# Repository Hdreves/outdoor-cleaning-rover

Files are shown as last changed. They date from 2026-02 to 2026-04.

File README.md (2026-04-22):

# Outdoor Cleaning Rover

## Project Description

Outdoor Cleaning Rover is a shoebox-sized keyboard/webpage controlled robot designed to patrol a patio and sidewalk and collect dog waste using a small “garbage-truck” style scoop. The rover navigates outdoors at low speed and can pickup waste when seen on camera. The project integrates embedded control, sensing, and vision hardware, powered through a LiPo battery.

**High-level goals**
- Drive safely on concrete/pavers.
- Detect a target/object and perform a pickup routine.
- Deposit waste into a bin for easy removal.

---

## Problem Domain

Pet waste on patios and sidewalks is unpleasant, unsanitary, and easy to miss especially at night or when the yard/patio is large. Owners often delay cleanup, which can create health risks (bacteria/parasites), odors, and messy tracking into the home. A small rover that can periodically patrol and collect waste reduces the burden on owners and keeps outdoor spaces clean.

---

## Features and Requirements

### Features & Requirements

1. Remote Control
   - Controlled through a webpage or keyboard

2. Pickup Mechanism (Garbage-Truck Scoop)
   - A front scoop lowers, collects waste, and deposits into a bin

3. Interactive Webpage
   - Updates with rover movements and sensor readings

4. Power Management
   - Battery-powered operation with regulated rails for logic and actuators

---

## Architecture

### System Overview

- **ESP32 (3.3V)** — Main controller (“brains”)
  - High-level behavior/state machine
  - Sensor fusion / navigation logic
  - Receives commands from Raspberry Pi
  - Sends motor/servo commands
 
- **Raspberry Pi** — Web interface, camera streaming, and high-level user interaction
  - Hosts the webpage/control dashboard
  - Streams live camera feed from the Pi Camera
  - Sends user control commands to the ESP32
  - Displays rover status and sensor feedback

- **Motor Driver (Dual H-Bridge)**
  - Drives left and right DC gear motors

- **Sensors**
  - ToF distance sensor for obstacle detection
  - Wheel encoders (for distance/heading estimation)

- **Actuators**
  - DC motors (drive)
  - Servo

- **Power**
  - 3S battery → main switch
  - Buck converter to regulated 5V rail
  - Motors powered from battery rail (through driver), logic from regulated rail
  - Common ground shared across all modules

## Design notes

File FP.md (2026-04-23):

---
marp: true
theme: default
paginate: true
size: 16:9
---

# CSC 494 Final Presentation  
## Outdoor Cleaning Rover

**Hunter Dreves** 

**CSC 494**  

---

# Project Overview

## Problem Domain
Outdoor pet waste cleanup.

 The goal was to create a rover that can move around outside, perform the task of picking up pet waste, and put it in a bin. This prevents having to do it manually by hand and dealing with the cleanup. This problem combined power distribution, mechanical design, sensing, and control logic in order to come up with a solution.

---

# Solution Domain

A robotic system that combines hardware and software to perform the task of waste cleanup.

My solution uses a small rover with motors, a scoop/dump mechanism powered by a servo, a breadboard housing ESP32 and VL53L0X sensor, a Raspberry Pi, DC convertors for Pi and servo, and a camera to see where the rover is moving.

---

# Progress Since S1P

## At S1P
- chassis was assembled
- Raspberry Pi was set up with camera and SSH
- breadboard and wiring were partially started

## FP
- Week 1: Soldered and wired sensors, started designing parts
- Week 2: Created webpage to interface with rover, started main electrical wiring
- Week 3: Continued creating webpage while waiting for parts
- Week 4: Created wires and wire connectors

---
# Progress Since S1P

## FP
- Week 5: Re-created custom parts, finished all main wiring
- Week 6: Created sketch for ESP32, put everything together
- Week 7: Began testing and working out bugs
- Week 8: Testing and working out bugs
---

## Project links
- **Canvas:** https://nku.instructure.com/courses/88152/pages/individual-progress-hunter-dreves
- **GitHub:** https://github.com/Hdreves/outdoor-cleaning-rover/tree/main

---

# Movement Demo

[Open this file on GitHub](https://github.com/Hdreves/outdoor-cleaning-rover/blob/main/Media/Demos/Movement.mp4)

---

# Scooping Demo

[Open this file on GitHub](https://github.com/Hdreves/outdoor-cleaning-rover/blob/main/Media/Demos/Scooping.mp4)

---

# Dumping Demo

[Open this file on GitHub](https://github.com/Hdreves/outdoor-cleaning-rover/blob/main/Media/Demos/Dumping.mp4)

---

# Webpage 1

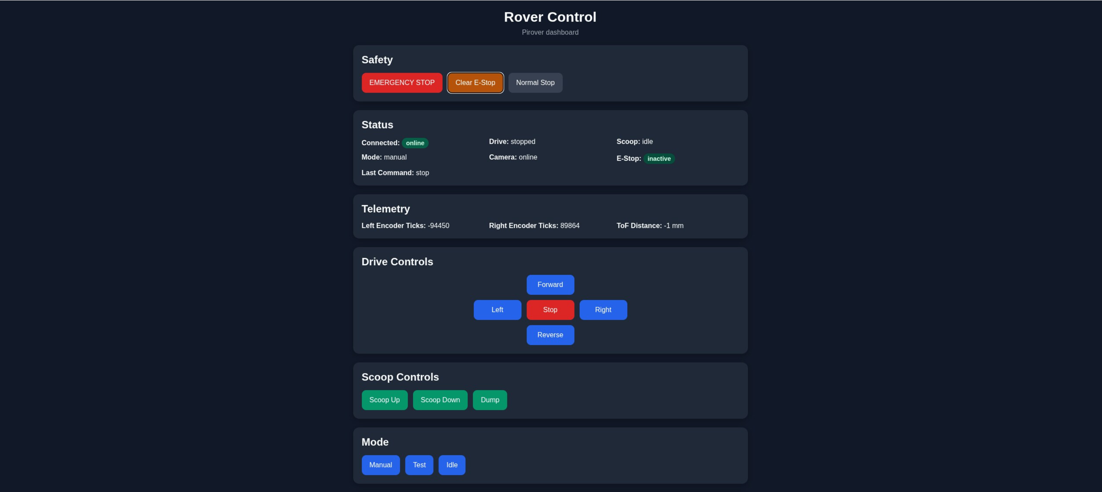
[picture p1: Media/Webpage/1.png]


---

# Webpage 2

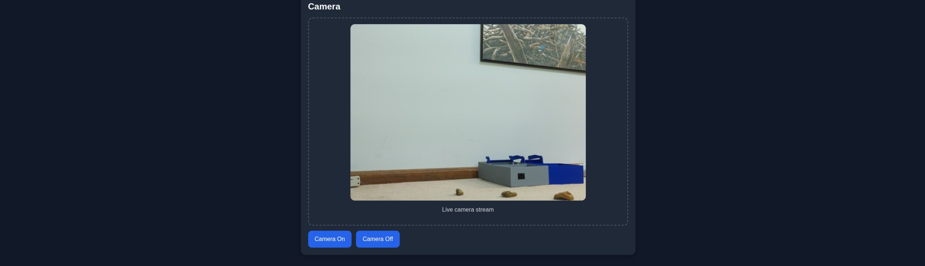
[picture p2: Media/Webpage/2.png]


---

# Learning With AI

## AI helped with
- Control logic design
- Debugging motors, sensors, and servo behavior
- Power distribution planning
- Code/setup guidance for integration

## Main lessons
- AI is useful for speeding up debugging
- AI struggles with mechanical designs
- AI is best used as a tool for support

---
# Topic 1

## Control Logic

The main takeaways when it comes to control logic is High level commands (Pi) need to be separated from low level commands (ESP32), pins need to be properly placed on ESP32, and not trying to force too much PWM control. With the Pi and ESP32 separated, debugging becomes much easier because you can isolate your issues. Also, ESP32 is much better at handling real time controls as that's what it was intended to do. Without proper pin placements, control goes out the window. You will run into problems like wrong motor movements, only one side moving, or nothing happening at all. When too many devices are being controlled through PWM, the devices will not function properly. Both devices are competing for timers/frequencies and in most cases one dominates the other. Also, devices use different timers/frequencies. For example, my servo (lower Hz) and DC motors (higher Hz), which lead to only the motors working. 

---
# Topic 2

## Power Distribution

The main takeaways when it comes to power distribution is sharing common ground, using convertors for lower rated electronics, and capacitors to prevent voltage spikes and drops. Without common ground signals are unreliable, sensors won't read or give bad values, random movements occur, or electrical damage. Without the use of convertors, a high voltage battery can fry your circut boards. The lower rated components can't handle the voltage supplied by the battery leading to failures and broken components. Capactitors come in handy for servos because sometimes voltage spikes and suddenly drops. During a voltage spike the capacitor stores that energy, and releases it during a moment of voltage drop.

---

# Issues Encountered and Solutions

## Issue 1: Wiring 
- Sensors not showing
- Wiring space
- Need for specific wires

## Solutions
- Used AI to determine sensor wasn't on shared ground
- Asked AI to help determine the dimensions for the box housing the elctrical components
- Had to cut, strip, and crimp the wires for my use case

--- 

## Issue 2: Hardware/Software Integration
- Motors moving incorrectly
- Values updating improperly
- Wheels continuosly moved after powering
- Servo wouldn't move

## Solutions
- Motors needed to be inverted
- Used AI to diagnose that there was interference when trying to use PWM for both the servo and motors. Moved the motors off of PWM and used digital direction signals through the motor driver instead.
---

## Issue 3: Design
- Initial design was much too complex
- Lack of space
- Reprint parts multiple times

## Soltuions
- Simplified the design
- Made space in any way possible, through creating holes and routing wires through them
- Modified incorrect parts and reprinted

---

# Questions

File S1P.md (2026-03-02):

---
marp: true
size: 4:3
paginate: true
---

# S1P  
## Outdoor Cleaning Rover

Hunter Dreves  

---

## Sprint 1 Progress

 **Chassis assembly**
- Rover chassis assembled (mechanical foundation complete)

 **Raspberry Pi Cam set up**
- SSH access configured for headless
- Camera connected and tested

 **Electronics groundwork**
- Breadboard layout for ESP (waiting on sensors should be in on 3/4)
- Planned separation of logic, servo, and motor power rails for safety

---

## Sprint 1 Progress

**Learned about hardware components and reliable power**
- 3s Lipo Battery (expected 3/4)
- 35 Kg servo (scoop and lift)
- 25 Kg servo (dump)
- VL53L0X TOF Sensors (2 meters, expected 3/4)
- 6V Buck converter for servos
- 5V Buck convertor for Pi
- Fuses
- Raspberry Pi (with Camera Module 3)

---

## Sprint 1 Progress
- Raspberry Pi (detection and navigation logic)
- ESP32-C6 (servos)

---

## Sprint 1 Learning with AI

### 1) Driving Controls
- Learned how control can be split between:
  - High-level decisions on Raspberry Pi (state machine)
  - Low-level motor/servo control (ESP32)

### 2) Power and Safe Wiring
- Learned importance of:
  - Separate power rails (motor vs servo vs logic)
  - Common ground
  - Fusing and switching
  - Avoiding brownouts

---

## What Changed From My Original Plan?

---

## Sprint 2 Final Goal

By end of Sprint 2, I will deliver a rover that:

- Manual control 
- Streams camera video from Raspberry Pi  
- Reads distance sensors for obstacle avoidance  
- Actuates the scoop mechanism on command  

**Stretch goals**
- Semi-autonomous navigation
- Target Detection

---

## Sprint 2 Plan

- Build 3-rail power architecture:
  - Motor rail (battery → fuse → switch → motor driver → motors)
  - Servo rail (battery → fuse → switch → 6V buck → servos)
  - Logic rail (battery → fuse → switch → 5V buck/USB-C → Pi + logic)
- Common ground + verify stability under load

---

## Sprint 2 Plan
- Wire VL53L0X ToF sensors on I2C
- Build UI for control
- Controlled tests

---

## Questions?

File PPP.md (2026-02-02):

---
marp: true
title: Outdoor Cleaning Rover — Project Plan
theme: default
paginate: true
size: 16:9
---

# Outdoor Cleaning Rover
## Project Plan Presentation (PPP)

**Shoebox-sized autonomous rover that patrols patio/sidewalk and collects dog waste** 

**Hunter Dreves
 CSC 494**

---

## Problem & Motivation

- Pet waste on patios/sidewalks is unsanitary and easy to miss
- Manual cleanup is time-consuming and often delayed
- A small rover can:
  - Patrol routinely
  - Avoid obstacles safely
  - Perform a pickup cycle

---
## Topics to Learn With AI

**Software:** Finite State Machines
  - Keeps the rovers movements organized and predictable.
  Prevents actions from overlapping and leadiing to errors.

**Hardware:** Power Distribution
  - Motors and servos create voltage dips.
  Without solid power distribution there 
  can be an increase in glitches.

---

## Sprint 1

- **How to power everything safely**
  - battery basics, turning the robot on/off, and keeping the electronics stable

- **How to make the rover move reliably**
  - drive forward/backward/turn and keep it controllable at a slow, safe speed

- **How to connect and read sensors**
  - distance sensors to “see” obstacles and bumpers as an emergency stop

- **How to test and troubleshoot**

---

## Sprint 2

- **Build the rover and pickup system**
  - a shoebox sized robot with a front scoop and a small bin so the rover can collect waste and store it

- **Make the scoop move automatically**
  - program the scoop to go down, collect, dump into the bin, then reset

- **Connect everything into one complete system**
  - the rover drives, stops when needed, picks up, then continues patrolling

---
## Sprint 2 (cont.)
- **Test outside and improve reliability**
  - run repeated outdoor tests and fix movement issues

- **Full Demo**
  - complete working system that collects and disposes waste

---
## Project Goals

**1. Safe Autonomous Movement**
- Drives on concrete and wood at low speed
- Avoids obstacles and stops on contact

**2. Reliable Pickup Mechanism**
- Scoop lowers, collects, dumps into bin, resets

**3. Demo**
- Successful pick up and removal

---

## Key Features

1. **Autonomous Patrol** 

2. **Obstacle Avoidance** 

3. **Physical Fail-Safe** 

4. **Pickup Sequence** 

5. **Status Feedback** 

---

## System Architecture

- **ESP32 (3.3V):** main logic + state machine + Wi-Fi
- **Arduino Nano (5V):** optional real-time I/O (servo PWM, encoders)
- **Motor Driver:** dual H-bridge for DC motors
- **Sensors:** ToF (front/left/right), bumpers, encoders
- **Actuators:** DC motors, servos
- **Power:** 2S battery → fuse → switch → buck converter (5V)

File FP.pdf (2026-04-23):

## CSC 494 Final Presentation

### Outdoor Cleaning Rover

Hunter Dreves
CSC 494

## Project Overview

### Problem Domain

Outdoor pet waste cleanup.
The goal was to create a rover that can move around outside, perform the task of picking up pet waste, and put it in a bin. This prevents having to do it manually by hand and dealing with the cleanup. This problem combined power distribution, mechanical design, sensing, and control logic in order to come up with a solution.

## Solution Domain

A robotic system that combines hardware and software to perform the task of waste cleanup.
My solution uses a small rover with motors, a scoop/dump mechanism powered by a servo, a breadboard housing ESP32 and VL53L0X sensor, a Raspberry Pi, DC convertors for Pi and servo, and a camera to see where the rover is moving.

## Progress Since S1P

### At S1P

chassis was assembled
Raspberry Pi was set up with camera and SSH
breadboard and wiring were partially started
FP

Week 1: Soldered and wired sensors, started designing parts
Week 2: Created webpage to interface with rover, started main electrical wiring
Week 3: Continued creating webpage while waiting for parts
Week 4: Created wires and wire connectors | 4

## Progress Since S1P

FP

Week 5: Re-created custom parts, finished all main wiring Week 6: Created sketch for ESP32, put everything together Week 7: Began testing and working out bugs
Week 8: Testing and working out bugs

### Project links

Canvas: https://nku.instructure.com/courses/88152/pages/individual-progress-hunter-dreves (https://nku.instructure.com/courses/88152/pages/individual-progress-hunter-dreves)
GitHub: https://github.com/Hdreves/outdoor-cleaning-rover/tree/main

## Movement Demo

Open this file on GitHub (https://github.com/Hdreves/outdoor-cleaning-rover/blob/main/Media/Demos/Movement.mp4)

## Scooping Demo

Open this file on GitHub (https://github.com/Hdreves/outdoor-cleaning-rover/blob/main/Media/Demos/Scooping.mp4)

## Dumping Demo

Open this file on GitHub (https://github.com/Hdreves/outdoor-cleaning-rover/blob/main/Media/Demos/Dumping.mp4)

## Webpage 1

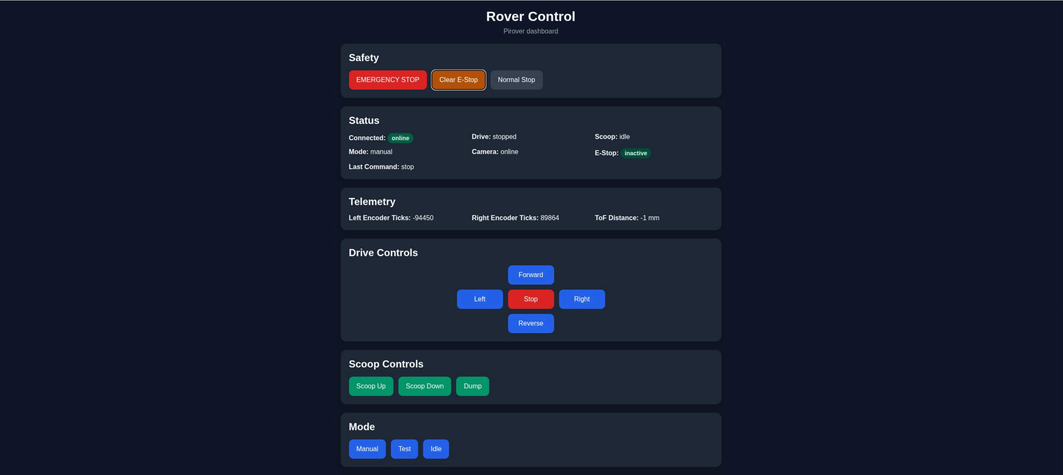
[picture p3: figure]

## Webpage 2

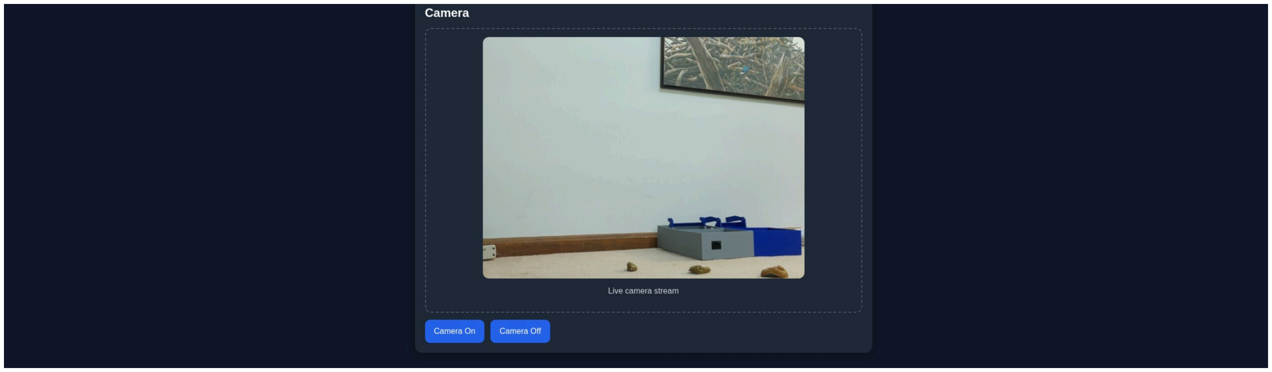
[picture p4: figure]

## Learning With AI

### AI helped with

Control logic design
Debugging motors, sensors, and servo behavior Power distribution planning
Code/setup guidance for integration

### Main lessons

AI is useful for speeding up debugging
AI struggles with mechanical designs
AI is best used as a tool for support | 12

## Topic 1

### Control Logic

The main takeaways when it comes to control logic is High level commands (Pi) need to be separated from low level commands (ESP32), pins need to be properly placed on ESP32, and not trying to force too much PWM control. With the Pi and ESP32 separated, debugging becomes much easier because you can isolate your issues. Also, ESP32 is much better at handling real time controls as that's what it was intended to do. Without proper pin placements, control goes out the window. You will run into problems like wrong motor movements, only one side moving, or nothing happening at all. When too many devices are being controlled through PWM, the devices will not function properly. Both devices are competing for timers/frequencies and in most cases one dominates the other. Also, devices use different timers/frequencies. For example, my servo (lower Hz) and DC motors (higher Hz), which lead to only the motors working.

## Topic 2

### Power Distribution

The main takeaways when it comes to power distribution is sharing common ground, using convertors for lower rated electronics, and capacitors to prevent voltage spikes and drops. Without common ground signals are unreliable, sensors won't read or give bad values, random movements occur, or electrical damage. Without the use of convertors, a high voltage battery can fry your circut boards. The lower rated components can't handle the voltage supplied by the battery leading to failures and broken components. Capactitors come in handy for servos because sometimes voltage spikes and suddenly drops. During a voltage spike the capacitor stores that energy, and releases it during a moment of voltage drop.

## Issues Encountered and Solutions

### Issue 1: Wiring

Sensors not showing
Wiring space
Need for specific wires

### Solutions

Used AI to determine sensor wasn't on shared ground
Asked AI to help determine the dimensions for the box housing the elctrical components
Had to cut, strip, and crimp the wires for my use case

### Issue 2: Hardware/Software Integration

Motors moving incorrectly
Values updating improperly
Wheels continuosly moved after powering Servo wouldn't move

### Solutions

Motors needed to be inverted
Used AI to diagnose that there was interference when trying to use PWM for both the servo and motors. Moved the motors off of PWM and used digital direction signals through the motor driver instead.

### Issue 3: Design

Initial design was much too complex Lack of space
Reprint parts multiple times

### Soltuions

Simplified the design
Made space in any way possible, through creating holes and routing wires through them
Modified incorrect parts and reprinted

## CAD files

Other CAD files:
3D Models/Arm v1.f3d
3D Models/Arm v2.f3d
3D Models/Bucket v1.f3d
3D Models/Bucket v2.f3d
3D Models/Dump Link.f3d
3D Models/Final Connectors.f3d
3D Models/Final Electronics Bin.f3d
3D Models/Final Scoop.f3d
3D Models/Final Support.f3d
3D Models/Final Top Bin.f3d
3D Models/Rear Arm Pivot Bracket.f3d

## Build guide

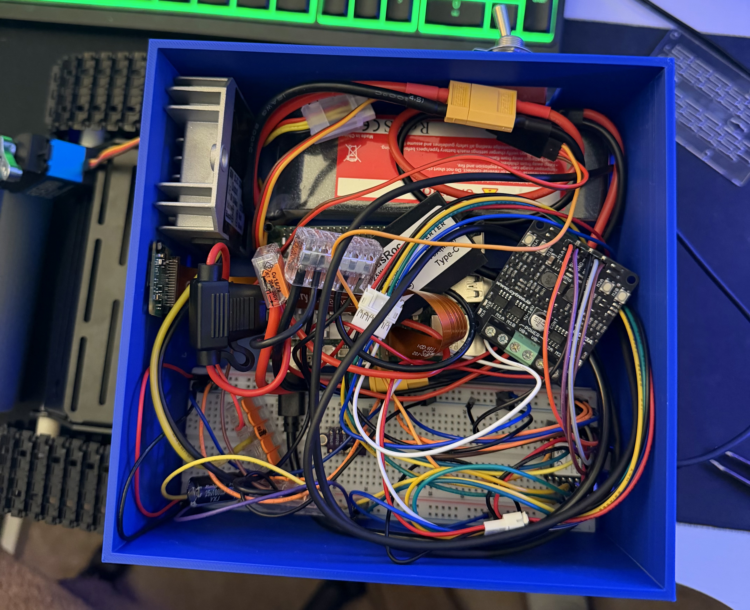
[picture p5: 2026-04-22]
Media/Wiring/Fully Wired.jpeg

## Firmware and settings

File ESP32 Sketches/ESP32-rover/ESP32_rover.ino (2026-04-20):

#include <Arduino.h>
#include <Wire.h>
#include <VL53L0X.h>
#include <ESP32Servo.h>

// =====================================================
// PIN MAP - BREADBOARD WIRING
// =====================================================
// Right motor driver pins (M1 side)
constexpr int PIN_RIGHT_MOTOR_A = D0;   // M1A
constexpr int PIN_RIGHT_MOTOR_B = D1;   // M1B

// Left motor driver pins (M2 side)
constexpr int PIN_LEFT_MOTOR_A  = D2;   // M2A
constexpr int PIN_LEFT_MOTOR_B  = D3;   // M2B

// ToF
constexpr int PIN_I2C_SDA = D4;
constexpr int PIN_I2C_SCL = D5;

// Servo
constexpr int PIN_SERVO = D6;

// RIGHT encoder (M1 side motor, looking from rear of rover)
constexpr int PIN_RIGHT_ENC_A = D7;     // yellow
constexpr int PIN_RIGHT_ENC_B = D8;     // green

// LEFT encoder (M2 side motor, looking from rear of rover)
constexpr int PIN_LEFT_ENC_A  = D9;     // yellow
constexpr int PIN_LEFT_ENC_B  = D10;    // green

// =====================================================
// CONFIG
// =====================================================
constexpr int SERIAL_BAUD = 9600;

// To fix incorrect motor movements
constexpr bool INVERT_LEFT_MOTOR = false;
constexpr bool INVERT_RIGHT_MOTOR = true;

// Servo config
constexpr int SERVO_MIN_US = 500;
constexpr int SERVO_MAX_US = 2500;
constexpr int SERVO_START_DEG = 0;

constexpr int SCOOP_DOWN_DEG = 10;
constexpr int SCOOP_UP_DEG   = 170;
constexpr int SCOOP_DUMP_DEG = 180;

constexpr uint32_t SERVO_UPDATE_MS = 20;
constexpr int SERVO_STEP_DEG = 2;

constexpr uint32_t TOF_UPDATE_MS = 50;

// =====================================================
// GLOBAL STATES
// =====================================================

VL53L0X tof;
bool tofOk = false;

Servo scoopServo;
String inputLine = "";

String driveState = "stopped";
String scoopState = "idle";
String modeState = "manual";
String cameraState = "offline";
String lastCommand = "none";

bool estopState = false;

volatile long leftTicks = 0;
volatile long rightTicks = 0;
int tofDistance = -1;

float currentLeftCmd = 0.0f;
float currentRightCmd = 0.0f;

int servoCurrentDeg = SERVO_START_DEG;
int servoTargetDeg = SERVO_START_DEG;

bool scoopMotionEnabled = false;

uint32_t lastServoUpdateMs = 0;
uint32_t lastTofUpdateMs = 0;

// =====================================================
// ENCODER ISR HELPERS
// =====================================================

void IRAM_ATTR leftEncA_ISR() {
  bool a = digitalRead(PIN_LEFT_ENC_A);
  bool b = digitalRead(PIN_LEFT_ENC_B);
  leftTicks += (a == b) ? 1 : -1;
}

void IRAM_ATTR leftEncB_ISR() {
  bool a = digitalRead(PIN_LEFT_ENC_A);
  bool b = digitalRead(PIN_LEFT_ENC_B);
  leftTicks += (a != b) ? 1 : -1;
}

void IRAM_ATTR rightEncA_ISR() {
  bool a = digitalRead(PIN_RIGHT_ENC_A);
  bool b = digitalRead(PIN_RIGHT_ENC_B);
  rightTicks += (a == b) ? 1 : -1;
}

void IRAM_ATTR rightEncB_ISR() {
  bool a = digitalRead(PIN_RIGHT_ENC_A);
  bool b = digitalRead(PIN_RIGHT_ENC_B);
  rightTicks += (a != b) ? 1 : -1;
}

// =====================================================
// MOTOR CONTROL
// =====================================================

void hardStopMotors() {
  currentLeftCmd = 0.0f;
  currentRightCmd = 0.0f;

  digitalWrite(PIN_LEFT_MOTOR_A, LOW);
  digitalWrite(PIN_LEFT_MOTOR_B, LOW);
  digitalWrite(PIN_RIGHT_MOTOR_A, LOW);
  digitalWrite(PIN_RIGHT_MOTOR_B, LOW);

  driveState = "stopped";
}

void driveMotorPins(int pinA, int pinB, float cmd, bool invert) {
  if (invert) {
    cmd = -cmd;
  }

  cmd = constrain(cmd, -1.0f, 1.0f);

  if (cmd > 0.01f) {
    digitalWrite(pinA, HIGH);
    digitalWrite(pinB, LOW);
  } else if (cmd < -0.01f) {
    digitalWrite(pinA, LOW);
    digitalWrite(pinB, HIGH);
  } else {
    digitalWrite(pinA, LOW);
    digitalWrite(pinB, LOW);
  }
}

void applyDriveOutputs() {
  driveMotorPins(PIN_LEFT_MOTOR_A,  PIN_LEFT_MOTOR_B,  currentLeftCmd,  INVERT_LEFT_MOTOR);
  driveMotorPins(PIN_RIGHT_MOTOR_A, PIN_RIGHT_MOTOR_B, currentRightCmd, INVERT_RIGHT_MOTOR);
}

void setDriveTank(float leftCmd, float rightCmd, const String& newState) {
  if (estopState) {
    return;
  }

  currentLeftCmd = constrain(leftCmd, -1.0f, 1.0f);
  currentRightCmd = constrain(rightCmd, -1.0f, 1.0f);
  applyDriveOutputs();
  driveState = newState;
}

void stopDrive() {
  hardStopMotors();
}

// =====================================================
// SERVO CONTROL
// =====================================================

void setScoopTarget(int targetDeg, const String& stateName) {
  if (estopState) {
    return;
  }

  servoTargetDeg = constrain(targetDeg, 0, 180);
  scoopState = stateName;
  scoopMotionEnabled = true;
}

void stopScoopMotion() {
  scoopMotionEnabled = false;

  if (servoCurrentDeg == SCOOP_DOWN_DEG) {
    scoopState = "down";
  } else if (servoCurrentDeg == SCOOP_UP_DEG) {
    scoopState = "up";
  } else if (servoCurrentDeg == SCOOP_DUMP_DEG) {
    scoopState = "dumped";
  } else {
    scoopState = "idle";
  }
}

void updateServoMotion() {
  uint32_t now = millis();
  if (now - lastServoUpdateMs < SERVO_UPDATE_MS) {
    return;
  }
  lastServoUpdateMs = now;

  if (!scoopMotionEnabled) {
    return;
  }

  hardStopMotors();

  bool moved = false;

  if (servoCurrentDeg < servoTargetDeg) {
    servoCurrentDeg = min(servoCurrentDeg + SERVO_STEP_DEG, servoTargetDeg);
    moved = true;
  } else if (servoCurrentDeg > servoTargetDeg) {
    servoCurrentDeg = max(servoCurrentDeg - SERVO_STEP_DEG, servoTargetDeg);
    moved = true;
  }

  if (moved) {
    scoopServo.write(servoCurrentDeg);
  }

  if (servoCurrentDeg == servoTargetDeg) {
    scoopMotionEnabled = false;

    if (servoTargetDeg == SCOOP_DOWN_DEG) {
      scoopState = "down";
    } else if (servoTargetDeg == SCOOP_UP_DEG) {
      scoopState = "up";
    } else if (servoTargetDeg == SCOOP_DUMP_DEG) {
      scoopState = "dumped";
    }
  }
}

// =====================================================
// TOF
// =====================================================

void initTof() {
  Wire.begin(PIN_I2C_SDA, PIN_I2C_SCL);
  tof.setTimeout(50);

  if (tof.init()) {
    tofOk = true;
    tof.setMeasurementTimingBudget(20000);
    tof.startContinuous(50);
  } else {
    tofOk = false;
    tofDistance = -1;
  }
}

void updateTof() {
  if (!tofOk) {
    return;
  }

  uint32_t now = millis();
  if (now - lastTofUpdateMs < TOF_UPDATE_MS) {
    return;
  }
  lastTofUpdateMs = now;

  uint16_t mm = tof.readRangeContinuousMillimeters();
  if (!tof.timeoutOccurred()) {
    tofDistance = (int)mm;
  }
}

// =====================================================
// STATUS / JSON
// =====================================================

void sendOk(const String& cmd) {
  Serial.print("{\"ok\":true,\"last_command\":\"");
  Serial.print(cmd);
  Serial.println("\"}");
}

void sendError(const String& msg) {
  Serial.print("{\"ok\":false,\"error\":\"");
  Serial.print(msg);
  Serial.println("\"}");
}

void sendPing() {
  Serial.println("{\"ok\":true,\"device\":\"xiao_esp32c6\",\"baud\":9600}");
}

void sendStatus() {
  long leftCopy, rightCopy;

  noInterrupts();
  leftCopy = leftTicks;
  rightCopy = rightTicks;
  interrupts();

  Serial.print("{");
  Serial.print("\"connected\":true,");
  Serial.print("\"drive\":\""); Serial.print(driveState); Serial.print("\",");
  Serial.print("\"scoop\":\""); Serial.print(scoopState); Serial.print("\",");
  Serial.print("\"mode\":\""); Serial.print(modeState); Serial.print("\",");
  Serial.print("\"camera\":\""); Serial.print(cameraState); Serial.print("\",");
  Serial.print("\"estop\":"); Serial.print(estopState ? "true" : "false"); Serial.print(",");
  Serial.print("\"left_ticks\":"); Serial.print(leftCopy); Serial.print(",");
  Serial.print("\"right_ticks\":"); Serial.print(rightCopy); Serial.print(",");
  Serial.print("\"tof_distance\":"); Serial.print(tofDistance); Serial.print(",");
  Serial.print("\"last_command\":\""); Serial.print(lastCommand); Serial.print("\"");
  Serial.println("}");
}

// =====================================================
// COMMAND PARSING
// =====================================================

float parseSpeedFromCommand(const String& line, float fallbackValue) {
  int lastSpace = line.lastIndexOf(' ');
  if (lastSpace < 0) {
    return fallbackValue;
  }

  String tail = line.substring(lastSpace + 1);
  float value = tail.toFloat();
  if (value <= 0.0f) {
    return fallbackValue;
  }

  return constrain(value, 0.0f, 1.0f);
}

void handleDriveCommand(const String& line) {
  if (estopState) {
    sendError("estop_active");
    return;
  }

  if (line.startsWith("DRIVE FORWARD")) {
    float speed = parseSpeedFromCommand(line, 0.50f);
    setDriveTank(speed, speed, "forward");
    lastCommand = "forward";
    sendOk(lastCommand);
  }
  else if (line.startsWith("DRIVE REVERSE")) {
    float speed = parseSpeedFromCommand(line, 0.50f);
    setDriveTank(-speed, -speed, "reverse");
    lastCommand = "reverse";
    sendOk(lastCommand);
  }
  else if (line.startsWith("TURN LEFT")) {
    float speed = parseSpeedFromCommand(line, 0.40f);
    setDriveTank(-speed, speed, "left");
    lastCommand = "left";
    sendOk(lastCommand);
  }
  else if (line.startsWith("TURN RIGHT")) {
    float speed = parseSpeedFromCommand(line, 0.40f);
    setDriveTank(speed, -speed, "right");
    lastCommand = "right";
    sendOk(lastCommand);
  }
  else if (line == "STOP" || line == "X") {
    stopDrive();
    lastCommand = "stop";
    sendOk(lastCommand);
  }
  else {
    sendError("unknown_drive_command");
  }
}

void handleScoopCommand(const String& line) {
  if (estopState) {
    sendError("estop_active");
    return;
  }

  hardStopMotors();

  if (line == "SCOOP UP") {
    setScoopTarget(SCOOP_UP_DEG, "raising");
    lastCommand = "scoop_up";
    sendOk(lastCommand);
  }
  else if (line == "SCOOP DOWN") {
    setScoopTarget(SCOOP_DOWN_DEG, "lowering");
    lastCommand = "scoop_down";
    sendOk(lastCommand);
  }
  else if (line == "SCOOP DUMP") {
    setScoopTarget(SCOOP_DUMP_DEG, "dumping");
    lastCommand = "dump";
    sendOk(lastCommand);
  }
  else if (line == "SCOOP STOP") {
    stopScoopMotion();
    lastCommand = "scoop_stop";
    sendOk(lastCommand);
  }
  else {
    sendError("unknown_scoop_command");
  }
}

void handleModeCommand(const String& line) {
  if (line == "MODE MANUAL") {
    modeState = "manual";
    lastCommand = "manual";
    sendOk(lastCommand);
  }
  else if (line == "MODE TEST") {
    modeState = "test";
    lastCommand = "test";
    sendOk(lastCommand);
  }
  else if (line == "MODE IDLE") {
    modeState = "idle";
    stopDrive();
    lastCommand = "idle";
    sendOk(lastCommand);
  }
  else {
    sendError("unknown_mode_command");
  }
}

void processCommand(String line) {
  line.trim();
  line.toUpperCase();

  if (line.length() == 0) {
    return;
  }

  // Support raw key aliases too
  if (line == "W") line = "DRIVE FORWARD";
  else if (line == "S") line = "DRIVE REVERSE";
  else if (line == "A") line = "TURN LEFT";
  else if (line == "D") line = "TURN RIGHT";
  else if (line == "X") line = "STOP";

  if (line == "PING") {
    sendPing();
  }
  else if (line == "STATUS") {
    sendStatus();
  }
  else if (line == "ESTOP") {
    estopState = true;
    stopDrive();
    scoopMotionEnabled = false;
    servoTargetDeg = servoCurrentDeg;
    scoopState = "idle";
    lastCommand = "emergency_stop";
    sendOk(lastCommand);
  }
  else if (line == "CLEAR ESTOP") {
    estopState = false;
    lastCommand = "clear_estop";
    sendOk(lastCommand);
  }
  else if (
    line.startsWith("DRIVE FORWARD") ||
    line.startsWith("DRIVE REVERSE") ||
    line.startsWith("TURN LEFT") ||
    line.startsWith("TURN RIGHT") ||
    line == "STOP"
  ) {
    handleDriveCommand(line);
  }
  else if (
    line == "SCOOP UP" ||
    line == "SCOOP DOWN" ||
    line == "SCOOP DUMP" ||
    line == "SCOOP STOP"
  ) {
    handleScoopCommand(line);
  }
  else if (
    line == "MODE MANUAL" ||
    line == "MODE TEST" ||
    line == "MODE IDLE"
  ) {
    handleModeCommand(line);
  }
  else {
    sendError("unknown_command");
  }
}

// =====================================================
// SAFETY
// =====================================================

void updateCommandWatchdog() {
  if (estopState) {
    stopDrive();
    return;
  }

  // Intentionally no auto-stop timeout here.
  // Rover keeps moving until a STOP command is received.
}

// =====================================================
// SETUP / LOOP
// =====================================================

void setup() {
  pinMode(PIN_LEFT_MOTOR_A, OUTPUT);
  pinMode(PIN_LEFT_MOTOR_B, OUTPUT);
  pinMode(PIN_RIGHT_MOTOR_A, OUTPUT);
  pinMode(PIN_RIGHT_MOTOR_B, OUTPUT);

  digitalWrite(PIN_LEFT_MOTOR_A, LOW);
  digitalWrite(PIN_LEFT_MOTOR_B, LOW);
  digitalWrite(PIN_RIGHT_MOTOR_A, LOW);
  digitalWrite(PIN_RIGHT_MOTOR_B, LOW);

  Serial.begin(SERIAL_BAUD);
  delay(100);

  hardStopMotors();
  delay(750);

  scoopServo.setPeriodHertz(50);
  scoopServo.attach(PIN_SERVO, SERVO_MIN_US, SERVO_MAX_US);
  scoopServo.write(SERVO_START_DEG);
  servoCurrentDeg = SERVO_START_DEG;
  servoTargetDeg = SERVO_START_DEG;

  pinMode(PIN_LEFT_ENC_A, INPUT_PULLUP);
  pinMode(PIN_LEFT_ENC_B, INPUT_PULLUP);
  pinMode(PIN_RIGHT_ENC_A, INPUT_PULLUP);
  pinMode(PIN_RIGHT_ENC_B, INPUT_PULLUP);

  attachInterrupt(digitalPinToInterrupt(PIN_LEFT_ENC_A), leftEncA_ISR, CHANGE);
  attachInterrupt(digitalPinToInterrupt(PIN_LEFT_ENC_B), leftEncB_ISR, CHANGE);
  attachInterrupt(digitalPinToInterrupt(PIN_RIGHT_ENC_A), rightEncA_ISR, CHANGE);
  attachInterrupt(digitalPinToInterrupt(PIN_RIGHT_ENC_B), rightEncB_ISR, CHANGE);

  initTof();

  hardStopMotors();

  Serial.println("{\"boot\":\"xiao_rover_ready\",\"baud\":9600}");
}

void loop() {
  while (Serial.available() > 0) {
    char c = (char)Serial.read();

    if (c == '\n' || c == '\r') {
      if (inputLine.length() > 0) {
        processCommand(inputLine);
        inputLine = "";
      }
    } else {
      inputLine += c;
    }
  }

  updateServoMotion();
  updateTof();
  updateCommandWatchdog();
}

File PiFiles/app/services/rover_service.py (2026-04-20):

from app.schemas import RoverStatus, ControlCommand
from app.services.serial_bridge import SerialBridge


class RoverService:
    def __init__(self, bridge: SerialBridge) -> None:
        self.bridge = bridge
        self.cached_status = RoverStatus()

    def ping(self) -> bool:
        try:
            reply = self.bridge.request_json("PING")
            ok = bool(reply.get("ok", False))
            self.cached_status.connected = ok
            return ok
        except Exception:
            self.cached_status.connected = False
            return False

    def get_status(self) -> RoverStatus:
        try:
            reply = self.bridge.request_json("STATUS")

            current_camera = self.cached_status.camera
            self.cached_status = RoverStatus(**reply)
            self.cached_status.camera = current_camera

        except Exception:
            self.cached_status.connected = False

        return self.cached_status

    def handle_command(self, cmd: ControlCommand) -> RoverStatus:
        action = cmd.action.strip().lower()

        if action == "forward":
            speed = cmd.value if cmd.value is not None else 0.35
            self.bridge.send_line(f"DRIVE FORWARD {speed:.2f}")
            self.cached_status.drive = "forward"

        elif action == "reverse":
            speed = cmd.value if cmd.value is not None else 0.35
            self.bridge.send_line(f"DRIVE REVERSE {speed:.2f}")
            self.cached_status.drive = "reverse"

        elif action == "left":
            speed = cmd.value if cmd.value is not None else 0.30
            self.bridge.send_line(f"TURN LEFT {speed:.2f}")
            self.cached_status.drive = "left"

        elif action == "right":
            speed = cmd.value if cmd.value is not None else 0.30
            self.bridge.send_line(f"TURN RIGHT {speed:.2f}")
            self.cached_status.drive = "right"

        elif action == "stop":
            self.bridge.send_line("STOP")
            self.cached_status.drive = "stopped"

        elif action == "scoop_up":
            self.bridge.send_line("SCOOP UP")
            self.cached_status.scoop = "raising"

        elif action == "scoop_down":
            self.bridge.send_line("SCOOP DOWN")
            self.cached_status.scoop = "lowering"

        elif action == "dump":
            self.bridge.send_line("SCOOP DUMP")
            self.cached_status.scoop = "dumping"
            
        elif action == "scoop_stop":
            self.bridge.send_line("SCOOP STOP")
            self.cached_status.scoop = "idle"

        elif action == "emergency_stop":
            self.bridge.send_line("ESTOP")
            self.cached_status.estop = True
            self.cached_status.drive = "stopped"

        elif action == "clear_estop":
            self.bridge.send_line("CLEAR ESTOP")
            self.cached_status.estop = False

        elif action == "manual":
            self.bridge.send_line("MODE MANUAL")
            self.cached_status.mode = "manual"

        elif action == "test":
            self.bridge.send_line("MODE TEST")
            self.cached_status.mode = "test"

        elif action == "idle":
            self.bridge.send_line("MODE IDLE")
            self.cached_status.mode = "idle"
            self.cached_status.drive = "stopped"

        elif action == "camera_on":
            self.cached_status.camera = "online"
            self.cached_status.last_command = action
            return self.cached_status

        elif action == "camera_off":
            self.cached_status.camera = "offline"
            self.cached_status.last_command = action
            return self.cached_status

        else:
            raise ValueError(f"Unknown action: {action}")

        self.cached_status.last_command = action
        return self.get_status()
